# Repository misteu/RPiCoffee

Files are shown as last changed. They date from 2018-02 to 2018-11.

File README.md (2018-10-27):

# RPiCoffee aka Coffee as a Service 4 real
Modding / hacking of a coffee machine (DeLonghi ECAM 22.110.B Magnifica S) for IoT capabilities 

See github-Page or docs/README.md for working progress: https://misteu.github.io/RPiCoffee/

Here is everything a little bit more detailed: https://github.com/misteu/RPiCoffee/wiki (<-- still a lot of stuff missing, coming soon!)

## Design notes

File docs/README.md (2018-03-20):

# RPiCoffee

This project's goal is to make a coffee machine responsive to different HTTP-Requests, like:

**JSON-Request**
```json
{
  "userID": "admin",
  "actions": [
    "turn on",
    "brew espresso"
  ]
}

```
'Cause nobody likes to wait for the machine.

_in fact: There are no JSONs involved right now :-D (see section "A little bit about [...]") Maybe in near future I will design a RESTful API supporting some cool JSON-responses like the one above_

see the project's wiki for more detailled information: [https://github.com/misteu/RPiCoffee/wiki](https://github.com/misteu/RPiCoffee/wiki)

**Possible scenarios are:**
- turn on and shutting down the machine via HTTP-request
- brewing single and double espresso via HTTP-request
- brewing single and double coffee via HTTP-request
- starting the rinse program via HTTP-request (good for preheating the system)
- chaining simple actions like in the example above
- reading out machine status (e.g. water level, coffee bean depot, temperature, errors, ...)
- rendering a responsive web-app for better user experience
- data logging and visualisation in the web-app

### Intro ###
The easiest way is to hack the existing frontpanel via overriding its pushbuttons. The HTTP-stuff can be handled by a microcontroller with a wifi-shield or a microcomputer like the the RaspberryPi Zero W which has built-in wifi.

I will stick to the Raspberry because it is cheap (around 12 Eur for the Zero W) and I do not have to make any hardware modifications to get it up and running. The Raspberry will be prepared with a minimal setup based on Raspbian Lite with everything unnecessary turned off. 

It's described in this article: [https://www.heise.de/ct/ausgabe/2017-22-Digitales-Flugblatt-Raspberry-Pi-mit-Batterie-als-anonymer-WLAN-Hotspot-und-Webserver-3851689.html](https://www.heise.de/ct/ausgabe/2017-22-Digitales-Flugblatt-Raspberry-Pi-mit-Batterie-als-anonymer-WLAN-Hotspot-und-Webserver-3851689.html)

The RPi will be powered by its own USB-power supply because I do not know how stable the coffee machines DC rails. Maybe later I will parallel the 230V rails of the coffee machine to the Raspberry's AC power supply.

On the RPi there will be running Flask for the HTTP-stuff and maybe a mongodb database for some data collecting.

### Mobile / Responsive User Interface stuff

#### WebApp-UI talking to the hardware
I combined my html+skeleton prototype with some Flask and the LED() function of the Python module gpiozero. In the animation below you can see one of the first iterations. All the buttons of the machine's front are accessible programatically right now. The "steam button" is not implemented in the WebApp because in general it is never used.

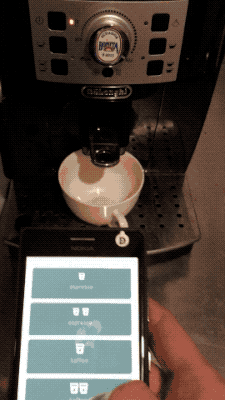
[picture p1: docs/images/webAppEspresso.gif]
animation of brewing espresso via Web App


The feature menus (statistics, settings and mining) are not implemented right now. I implemented a small java script popup to inform the user about that when one of these buttons is clicked.

I already installed mongoDB on the raspberry to save statistics and settings and made some first experiments.

+++ update +++

Instead of the fun but pretty useless mining, there is now implemented an info screen with train departure times. See section "API-Calls [...]" in my wiki.

#### Second iteration: WebApp-UI
I made a redesign of the UI because I did not like the dark theme (see below). I began prototyping the complete thing in Sketch and transfered it later to HTML and CSS with the help of Skeleton ([getskeleton.com](http://www.getskeleton.com)) and Sketch's CSS and SVG output-features. 

I picked a nice morning like gradient from [webgradients.com](http://webgradients.com) and played around with colorsets from [coolors.co]. For the final touch I added these transparent triangle things for some foggy morning effects. They are technically stacked CSS3 clipping paths of div-elements I colored with #fff and alpha = 0.2 ;-)

The icons are this time from Google's material design icon-font ([https://material.io/icons/](https://material.io/icons/)) I found them via the awesome iconfont plugin for Sketch by Kerem Sevencan ([https://github.com/keremciu](https://github.com/keremciu))

All the hover interaction-stuff and responsiveness is finished. Everything else (settings, stats and cryptomining😅) will be added iteratively as soon as main functionalities are up and running.

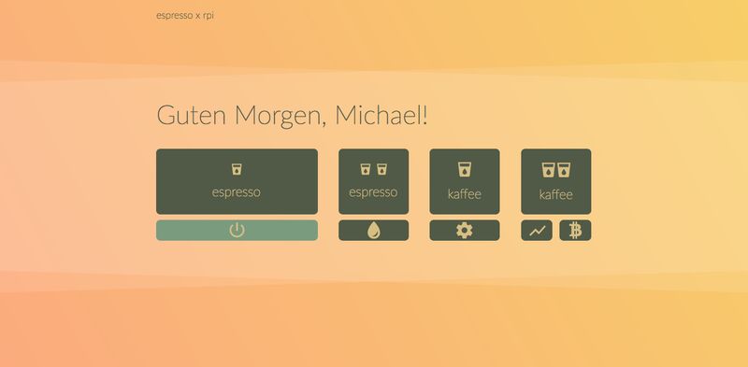
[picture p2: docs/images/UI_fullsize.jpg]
Image of new UI


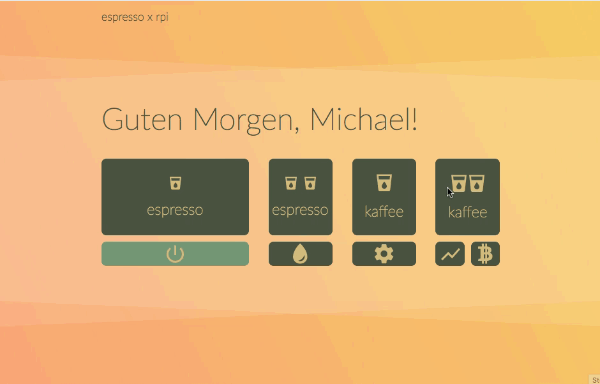
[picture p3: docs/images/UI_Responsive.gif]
Image of new UI


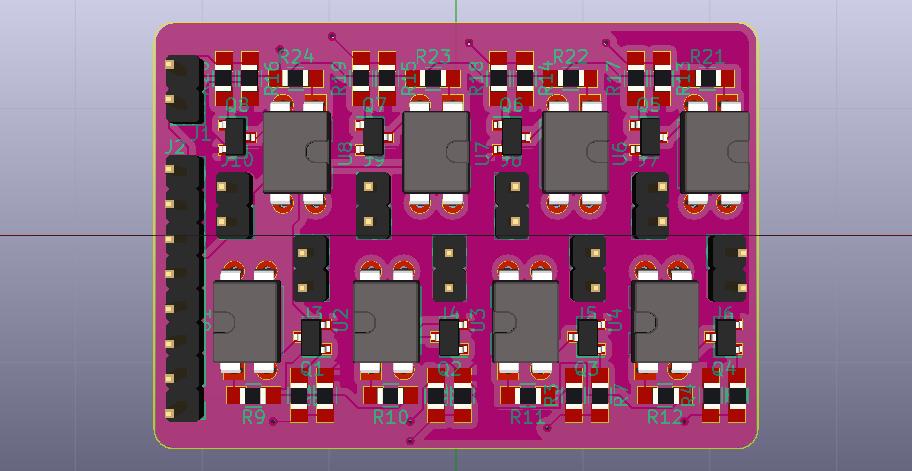
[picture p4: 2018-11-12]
schematics_KiCadProject/kaffeeInterface.jpg

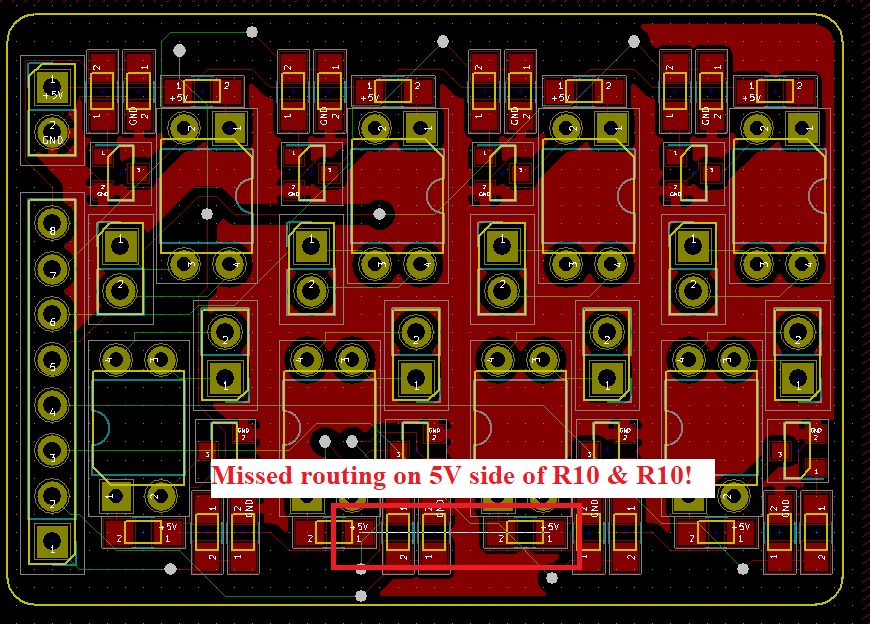
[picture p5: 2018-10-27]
schematics_KiCadProject/missedRouting.jpg

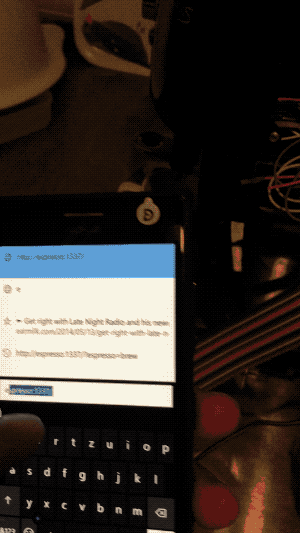
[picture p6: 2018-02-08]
docs/images/Flask_to_espresso.gif

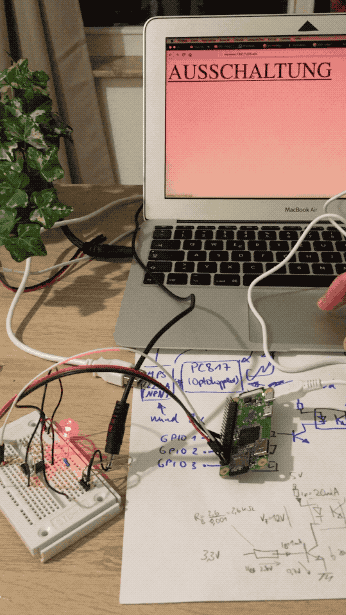
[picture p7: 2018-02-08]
docs/images/Flask_to_GPIO.gif

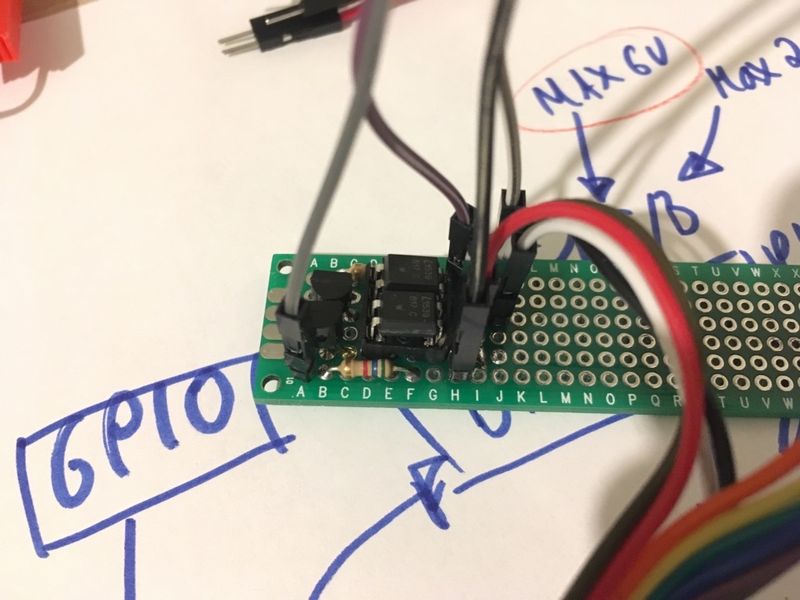
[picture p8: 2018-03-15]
docs/images/Optocoupler_circuit.jpg

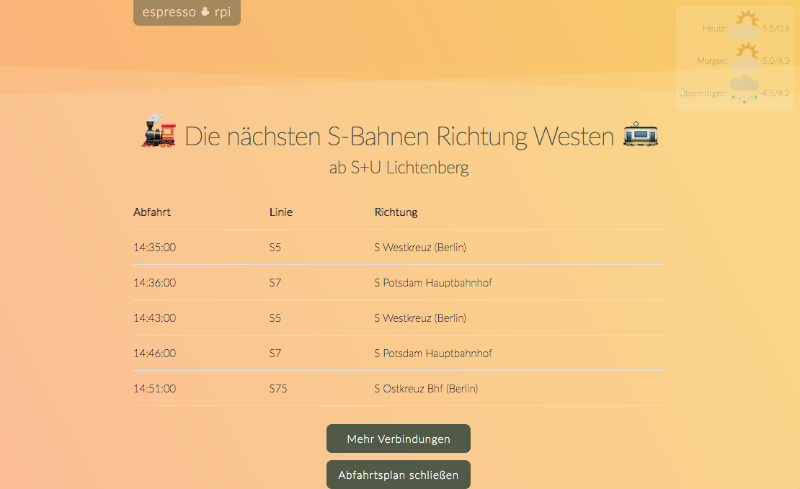
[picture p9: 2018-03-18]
docs/images/UI_metro_widget.png

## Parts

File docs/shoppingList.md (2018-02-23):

### Raspberry and power supply
1x Raspberry Pi Zero W 13,50€ (inkl. Versand, von pimoroni)
1x NT MUSB 2 WS
USB-Ladegerät, 5 V, 2000 mA, Micro-USB
6,00 €

### other stuff from reichelt (for the interface circuit)

3x
MOS 4051
CD4051BE
0,90 €

15x
LTV 817
OPTOKOPPLER
2,86 €

20x
BC 547A CDIL
Transistor NPN TO-92 45V 0,1A 0,5W
0,60 €

20x
1/4W 1,0K
Widerstand, Kohleschicht, 1,0 kOhm, 0207, 250 mW, 5%
0,67 €

20x
1/4W 4,7K
Widerstand, Kohleschicht, 4,7 kOhm, 0207, 250 mW, 5%
0,67 €

20x
1/4W 200
Widerstand, Kohleschicht, 200 Ohm, 0207, 250 mW, 5%
0,67 €

20x
1/4W 5,6K
Widerstand, Kohleschicht, 5,6 kOhm, 0207, 250 mW, 5%
0,67 €

5x 
WAGO 221-413
Verbindungsklemme, 3-Leiteranschluss
2,40 €

1x
H05VK 0,75-10BR
Schaltlitze H05V-K, 0,75 mm, 10 m, braun
1,85 €

1x
H05VK 0,75-10BL
Schaltlitze H05V-K, 0,75 mm, 10 m, blau
1,75 €

1x
SDH 1,6 SW
10er Pack 2:1 Schrumpfschlauch, 1,6mm schwarz
0,25 €

1x
SDH 2,4 RT
10er Pack 2:1 Schrumpfschlauch, 2,4mm rot
0,32 €

1x
SDH 3,2 SW
10er Pack 2:1 Schrumpfschlauch, 3,2mm schwarz
0,26 €

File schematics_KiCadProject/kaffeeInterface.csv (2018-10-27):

ID | Bezeichner | Gehäuse | Stückzahl | Bezeichnung | Anbieter und Ref.
1 | J1,J3,J4,J5,J6,J7,J8,J9,J10 | Pin_Header_Straight_1x02_Pitch2.54mm | 9 | Conn_01x02_Male
2 | J2 | Pin_Header_Straight_1x08_Pitch2.54mm | 1 | Conn_01x08_Male
3 | Q1,Q2,Q3,Q4,Q5,Q6,Q7,Q8 | SOT-23 | 8 | BC847
4 | R1,R2,R3,R4,R13,R14,R15,R16 | R_0805_HandSoldering | 8 | 10k
5 | R5,R6,R7,R8,R17,R18,R19,R20 | R_0805_HandSoldering | 8 | 5,6k
6 | R9,R10,R11,R12,R21,R22,R23,R24 | R_0805_HandSoldering | 8 | 200
7 | U1,U2,U3,U4,U5,U6,U7,U8 | DIP-4_W7.62mm | 8 | LTV-817

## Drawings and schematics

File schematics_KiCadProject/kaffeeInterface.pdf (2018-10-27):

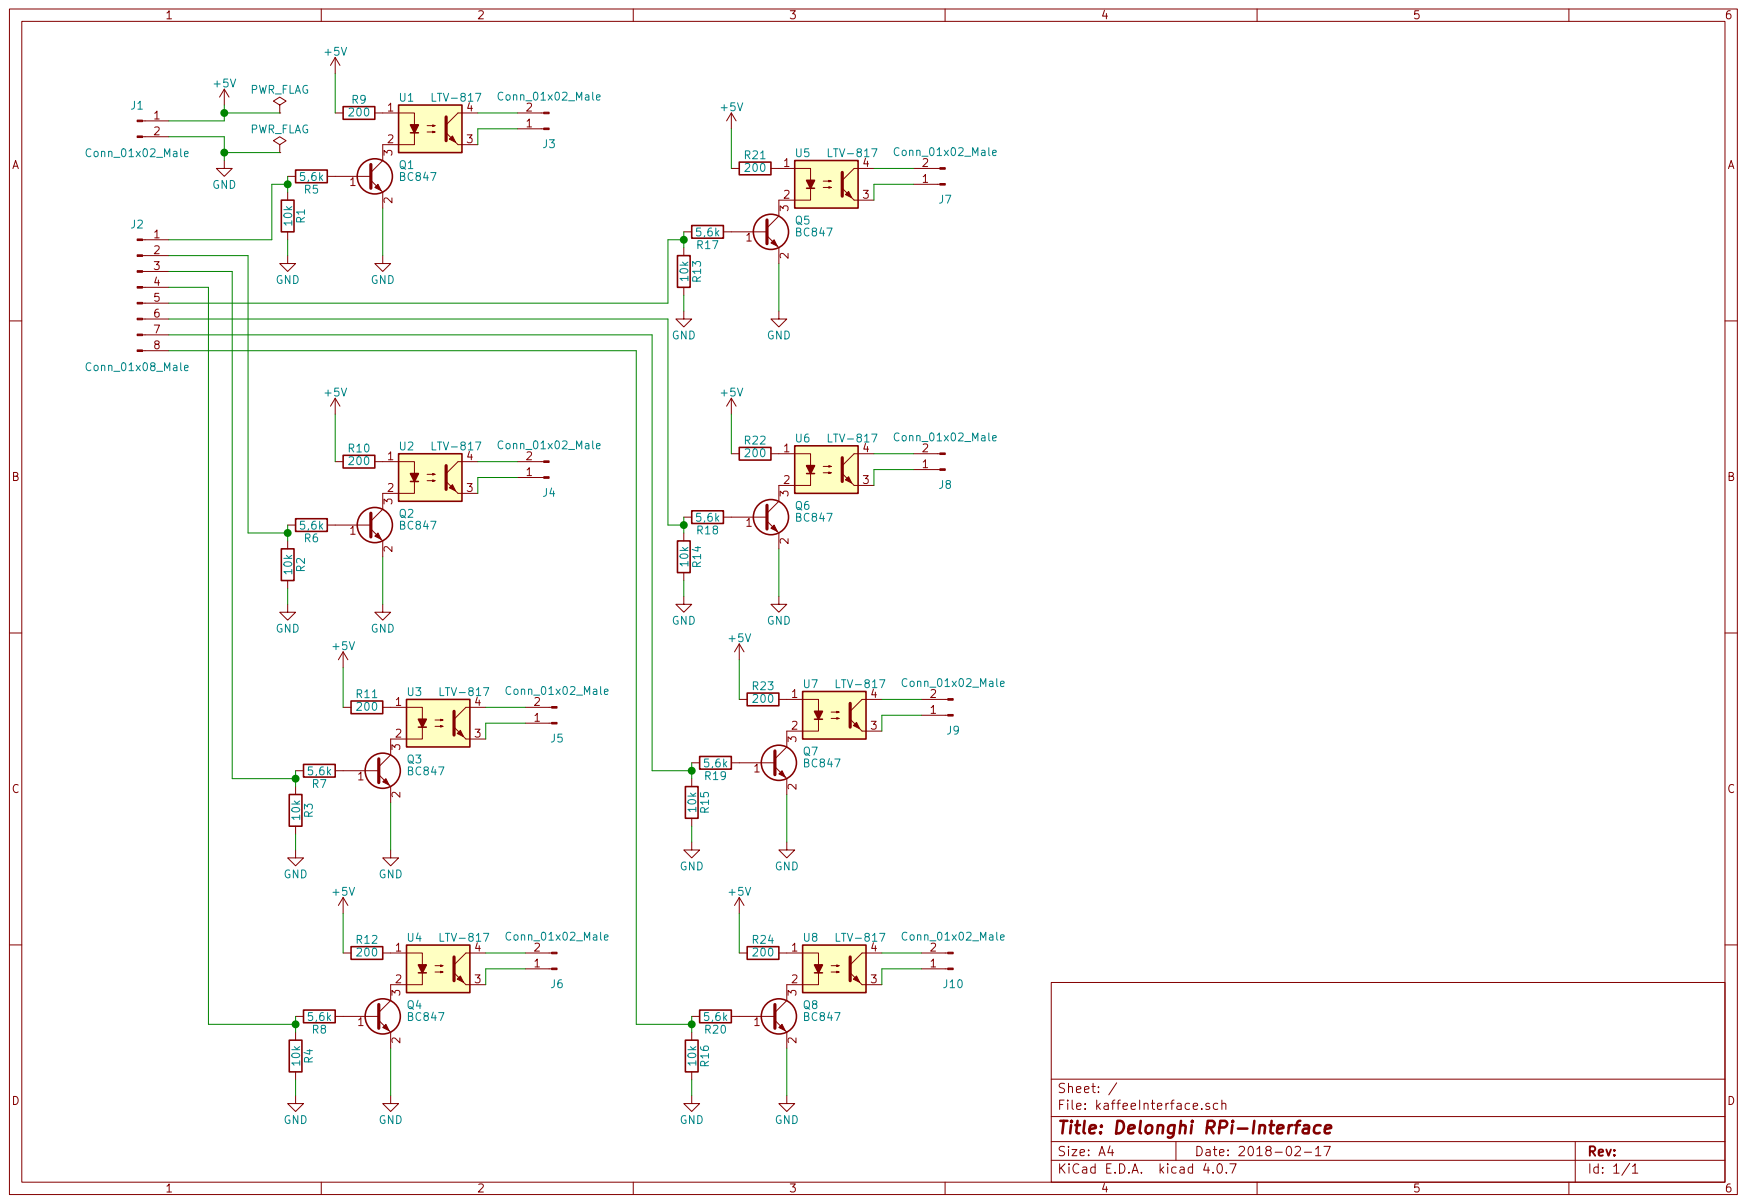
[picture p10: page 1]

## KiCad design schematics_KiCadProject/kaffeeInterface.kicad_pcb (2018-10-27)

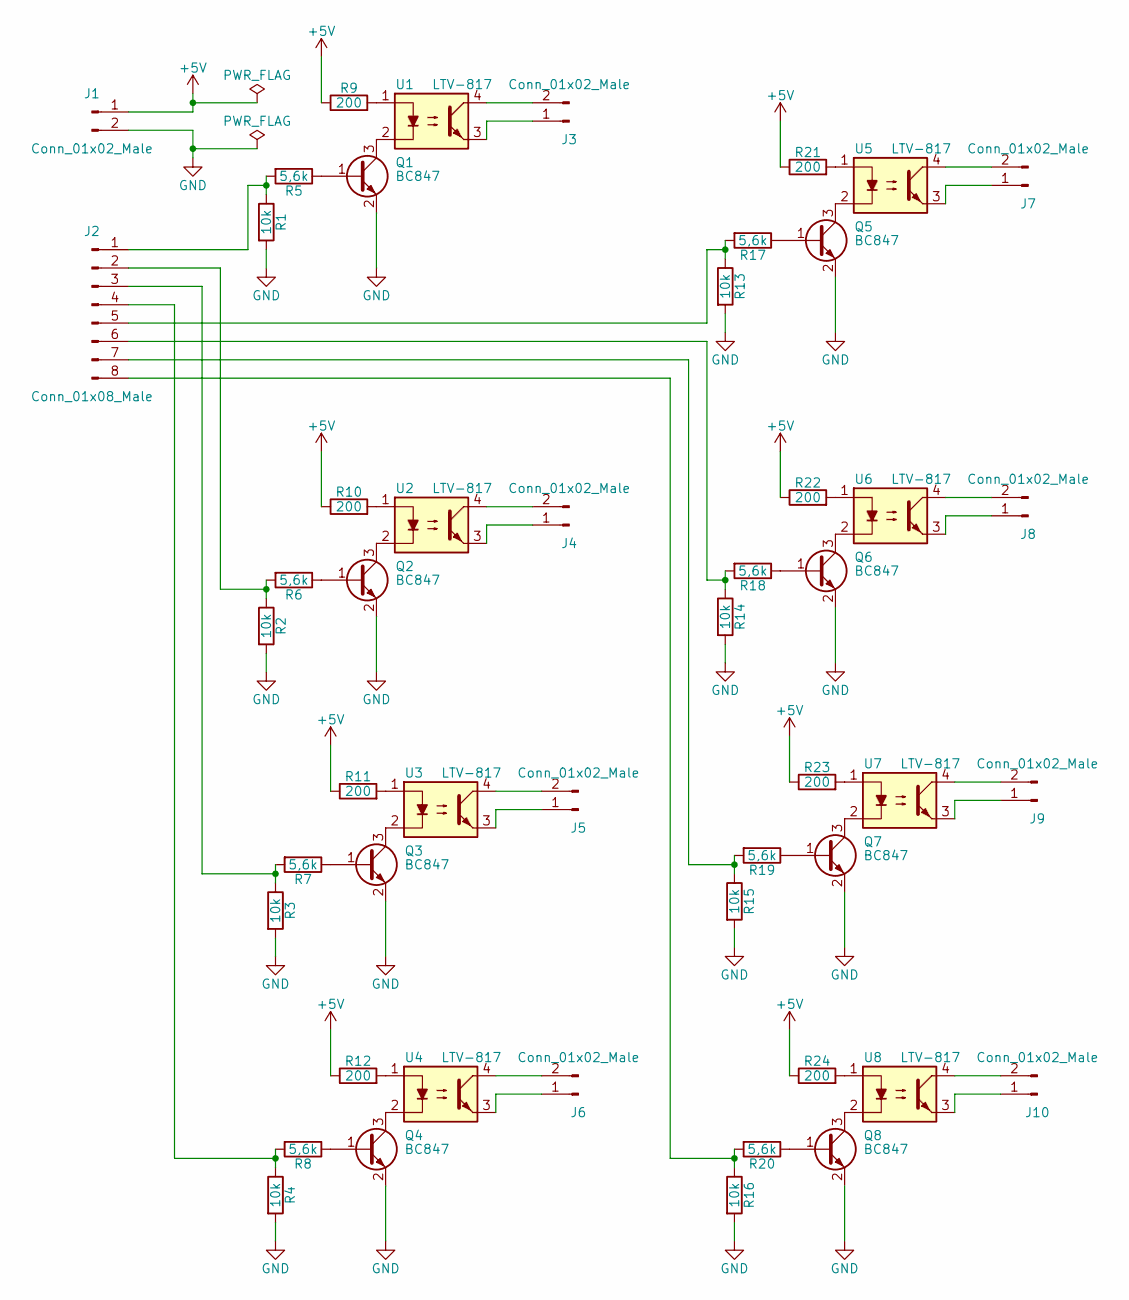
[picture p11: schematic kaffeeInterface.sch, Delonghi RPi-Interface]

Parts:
J1, J3, J4, J5, J6, J7, J8, J9, J10: Conn_01x02_Male; Pin_Header_Straight_1x02_Pitch2.54mm
J2: Conn_01x08_Male; Pin_Header_Straight_1x08_Pitch2.54mm
Q1, Q2, Q3, Q4, Q5, Q6, Q7, Q8: BC847; SOT-23
R1, R2, R3, R4, R13, R14, R15, R16: 10k; R_0805_HandSoldering
R5, R6, R7, R8, R17, R18, R19, R20: 5,6k; R_0805_HandSoldering
R9, R10, R11, R12, R21, R22, R23, R24: 200; R_0805_HandSoldering
U1, U2, U3, U4, U5, U6, U7, U8: LTV-817; DIP-4_W7.62mm

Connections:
+5V: J1.1, R9.1, R10.1, R11.1, R12.1, R21.1, R22.1, R23.1, R24.1
GND: J1.2, Q1.2 (E), Q2.2 (E), Q3.2 (E), Q4.2 (E), Q5.2 (E), Q6.2 (E), Q7.2 (E), Q8.2 (E), R1.2, R2.2, R3.2, R4.2, R13.2, R14.2, R15.2, R16.2
unnamed: J2.1, R1.1, R5.2
unnamed: J2.2, R2.1, R6.2
unnamed: J2.3, R3.1, R7.2
unnamed: J2.4, R4.1, R8.2
unnamed: J2.5, R13.1, R17.2
unnamed: J2.6, R14.1, R18.2
unnamed: J2.7, R15.1, R19.2
unnamed: J2.8, R16.1, R20.2
unnamed: J3.1, U1.3
unnamed: J3.2, U1.4
unnamed: J4.1, U2.3
unnamed: J4.2, U2.4
unnamed: J5.1, U3.3
unnamed: J5.2, U3.4
unnamed: J6.1, U4.3
unnamed: J6.2, U4.4
unnamed: J7.1, U5.3
unnamed: J7.2, U5.4
unnamed: J8.1, U6.3
unnamed: J8.2, U6.4
unnamed: J9.1, U7.3
unnamed: J9.2, U7.4
unnamed: J10.1, U8.3
unnamed: J10.2, U8.4
unnamed: Q1.1 (B), R5.1
unnamed: Q1.3 (C), U1.2
unnamed: Q2.1 (B), R6.1
unnamed: Q2.3 (C), U2.2
unnamed: Q3.1 (B), R7.1
unnamed: Q3.3 (C), U3.2
unnamed: Q4.1 (B), R8.1
unnamed: Q4.3 (C), U4.2
unnamed: Q5.1 (B), R17.1
unnamed: Q5.3 (C), U5.2
unnamed: Q6.1 (B), R18.1
unnamed: Q6.3 (C), U6.2
unnamed: Q7.1 (B), R19.1
unnamed: Q7.3 (C), U7.2
unnamed: Q8.1 (B), R20.1
unnamed: Q8.3 (C), U8.2
unnamed: R9.2, U1.1
unnamed: R10.2, U2.1
unnamed: R11.2, U3.1
unnamed: R12.2, U4.1
unnamed: R21.2, U5.1
unnamed: R22.2, U6.1
unnamed: R23.2, U7.1
unnamed: R24.2, U8.1

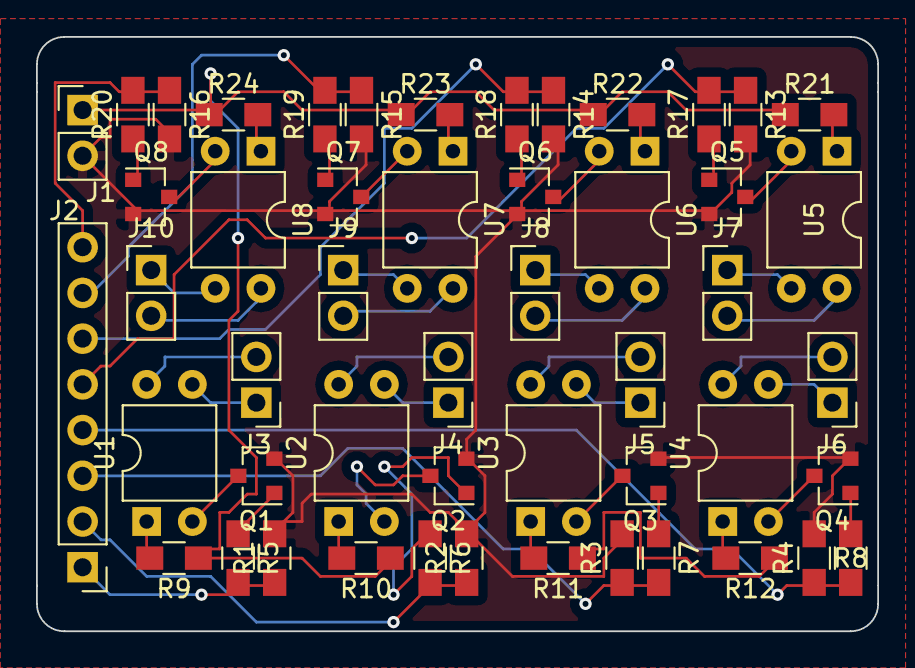
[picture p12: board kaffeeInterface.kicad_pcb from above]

Board: 2 copper layers, 46.7 x 33.0 mm, 50 parts (0 on the bottom side), 50 nets.

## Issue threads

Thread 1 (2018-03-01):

RFID payment system

adur1990, 2018-03-01:
Hi,

I had a somewhat similar idea with our coffee machine. We have the same DeLonghi machine. What we want to do is to have a system, which requires a RFID card to unlock the device. The normal buttons should not work anymore.

Now, we could do it with the same technique like you by interfacing the buttons, but it would be great, if we could reverse engineer the firmware and modify it like we want. And I saw in your todo list, that you also plan to interface all sensors and so on.

We have the schematics of the machine and the firmware (the schematics are in german, but as I can see, you are from Berlin). I will attach both to this issue. Maybe we can join forces :)
[DeLonghi_Magnifica_ECAM22.110_CH00.pdf](https://github.com/misteu/RPiCoffee/files/1770720/DeLonghi_Magnifica_ECAM22.110_CH00.pdf)
[PIC18LF2520_ECAM22.110_SW1.2.zip](https://github.com/misteu/RPiCoffee/files/1770721/PIC18LF2520_ECAM22.110_SW1.2.zip)

misteu, 2018-03-15:
Hi there!
Sorry for my late reply, unfortunately I saw your nice comment onyl now! Although I made some updates on github meanwhile... I will have to change my notification settings on github :-D

Your idea sounds great! And: WOW! Your schematics will help so much for updates in near future!
Until now I measured everything bit by bit with my cheapo voltmeter ;D

Reverse engineering sounds pretty decent!
One of my first ideas was to grab the signals between the machine's mainboard and the front PCB. Then I could have used the flat wire and some interface between the front PCB and the mainboard. But in the end, my bridging (hammer-like) approach feeled much easier for me :)

For reading the machine's sensors and getting feedback in general, the reverse engineering would be really, really nice.

On the other hand, I do not know if there is any real advantage of your second idea in modifying the firmware. In my opinion the results (espresso) of the machine's original behaviour are pretty good I think. Messing around with motor movements and so on bears the risk of crashing something more than electronics.

With my solution you could just cut or desolder the mechanical buttons and connect some RFID reader to the raspberry. Oh and I did not upload one of my schematics i do realize right now :-D
Will be added soon!

I will definitely use your schematics and look into your firmware. Thanks again! And I am totally into joining forces!

You have some experience with PICs? I did not yet look into the firmware but I spotted "PIC..." :-)

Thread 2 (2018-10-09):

Electronics tutorial

marciii, 2018-10-09:
Hi,

Ive seen this project and was really amazed and want to try it for my machine too.

However I have no clue about the electronics - how to connect the Pi and the machine in Detail.

Are you still planning to do a noob-friendly tutorial? Would ne awesome!

Cheers

rgerr, 2018-10-09:
+1, interested in this too.

rgerr, 2018-10-11:
Have checked out the shoppinglist, however it is incomplete. Firgured I would try and make it work through the pictures. But I can't seem to find the PCB board/interface where all the parts are soldered to.

misteu, 2018-10-26:
Sorry for my late response! I forgot to set any notifications on github.
Thank you very much for your feedback, it is nice to hear that you are interested!

Yeah, I will definitely work on a tutorial/rework the circuit diagrams. Currently, I am a little bit busy with my Masters thesis but I will find some time ;-)

marciii, 2018-10-26:
Nice, thanks!
And good luck with your thesis =)

rgerr, 2018-10-26:
Do you have the gerber files for the pcb? Then I can order it and try already!

misteu, 2018-10-27:
hi there,
I just uploaded the whole KiCad Project to the repo. My PCBs were made by Oshpark where you can upload your KiCad files directly without plotting gerber files. In case you want to use some other service, I exported the gerber plots in a separate folder.

I also included the schematic as PDF.

Please pay attention to the missing route between to resistor R10 and R11. I remarked that when the PCBs where already produced.  ou have to solder some wire by hand to fix that. I included a screenshot of KiCad where I marked that area. You can try to reroute it in KiCad or just fix it the same way ;)

Hope that helps so far!

misteu, 2018-10-27:
No it is not fixed.

You can fix it manually with soldering a wire as shown here: https://github.com/misteu/RPiCoffee/blob/master/schematics_KiCadProject/missedRouting.jpg

On that photo you can see how it looks on the finished PCB: https://github.com/misteu/RPiCoffee/blob/master/docs/images/PCB_soldered.jpg
So, pretty easy. If you managed to solder all the SMD stuff on the board, this one will be the most relaxing work ever 😅

If there is enough space on the PCB to fix that route, that would be the more elegant solution. But honestly, no one notices that PCB when it is built in 😄

rgerr, 2018-11-07:
Could you perhaps update the shopping list you created? Or it the shopping list actual, on Reichelt?

misteu, 2018-11-07:
hi there,
for soldering the interface circuit you just need the stuff I put into that table here in the wiki: https://github.com/misteu/RPiCoffee/wiki/Shopping-list

You will find all the parts if you search for them in your favorite electronics store. All of these are pretty common parts.

In addition to that you just need the RPI, a power supply and very thin wire as described in the wiki entry.

rgerr, 2018-11-08:
Thanks, ordered the PCBs. But I see that you updated the shopping list, now I am not able to find all the parts anymore on reichelt. Could you perhaps send me the actual reichelt list? Makes it allot easier to order for me.

misteu, 2018-11-10:
hi there.

You can still find everything on reichelt. Just type in the part number to the search field.

Pin headers straight are called "Stiftleiste" at reichelt. You can buy these: https://www.reichelt.de/rnd-stiftleiste-8-pol-rm-2-54-mm-rnd-205-00629-p208855.html?&trstct=pol_3

You can order them four times (1x 1x08 and 9x 01x02) and break them apart to get the 01x02 headers

The transistors (BC847) you need are these: https://www.reichelt.de/bipolartransistor-npn-45v-0-1a-0-3w-sot-23-rnd-bc847b-p223362.html?&trstct=pos_0
make sure you buy transistors with the case type called: SOT-23 (like in the link above)

The resistors you can find here: https://www.reichelt.de/0805/2/index.html?ACTION=2&LA=2&GROUPID=8397 You can find the right value via the filter on the left, you need 10k, 5.6k and 200 each one eight times. They cost pretty much nothing. So I would buy e.g. 100 of each value (1,2€ per value). They get lost easily and you can uses them for some other projects, too.

The optocouplers are these: https://www.reichelt.de/optokoppler-ltv-817-p76173.html?&trstct=pos_3

you can solder the optocouplers directly onto your PCB or use some sockets. I don't know if there are 4pin sockets available. I did not found them, so I cut apart these: https://www.reichelt.de/ic-sockel-8-polig-doppelter-federkontakt-gs-8-p8230.html?&trstct=pol_1

You can buy theses wires to connect/solder your front panel buttons to the interface PCB: https://www.reichelt.de/index.html?ACTION=446&LA=3&q=kupferlackdraht
I would not buy something thicker than 0.2mm because there is not much space if you want to connect all the buttons.

To connect the copper wires to your interface board's connectors I would use these wires, because they already have the right connector: https://www.reichelt.de/flexible-drahtbruecken-7-cm-buchse-buchse-10er-pack-steckboard-mbbvt-p177393.html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 just cut them apart and solder them to the copper wires.

Everything is pretty standard stuff so you could also look on ebay for cheaper offers. I ordered a lot of electronics parts on ebay.

I hope that helps.

rgerr, 2018-11-10:
Alright, thanks! So the parts you linked are all the parts I need, in the correct number?

misteu, 2018-11-10:
Yeah for the interface PCB that should work. I suggest you look at the circuit and do check if everything is on the list.

And of course you need the raspberry pi ;) You will also need some pin headers and jumper wires for connecting the raspberry pi to the interface PCB. There are also shops offering the raspberry pi with pre-soldered headers for a few euros more. If you buy a handful of jumper wires you have enough for soldering them to the copper wires and for connecting the PCB to your raspberry. Jumper wires with a length of 10cm are pretty good. I would buy 50 of them or something like that on ebay.

So I would not count every single piece of the circuit ;) Overall, the parts are pretty cheap, even if you buy everthing double ;)

rgerr, 2018-11-11:
Thanks! Ordered the parts. This is my first ‘big’ soldering project. Did a few small projects with Wemos and ESP8266.

Now when the parts are in, I can get started. Do you have a overview where I can easily see which part goes where?

misteu, 2018-11-11:
I looked in KiCad while soldering. Actually it's eight times the same circuit. So if you finished one or two of them you will know which part goes where ;-)

I reinstalled everything on my rpi today, because something crashed some weeks ago which made it inaccessible. I don't know why this did happen, maybe the logfiles grew to big or something like that.

Long story short: It's a good practice to make some kind of backup of your SD-card as soon as everything works. I didn't had that.. :( Spent some hours reinstalling everything by hand :-/
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
misteu, 2018-11-11:
ah nice! I didn't heard of Homebridge before :)

self-maintaining sounds great, I hacked something together on a fresh Raspian Jessie install.

haha I like that idea of connecting the machine via homebridge to siri 😄

rgerr, 2018-11-12:
Do you have a high resolution picture of the soldered PCB? I am having a hard time figuring out which goes where.

misteu, 2018-11-12:
Do you have KiCad installed? To look there is the safest way to solder the parts to the right spot.
There is also a 3D Model Viewer built-in. But I prefer the PCB view where you can just right click the connections and see which part goes there.

Anyway, I can make some photos today because I want to reinstall the updated RPI to the machine. But I can't promise high resolution pictures 😄

rgerr, 2018-11-12:
Currently, no. I will get to installing that. The KiCad files provided will generate a 3D model? That would be very helpful. The schematics are gibberish to me, when it comes to actually soldering the parts where they belong.

A few close up pictures of the circuits would be great, will make it a bit more 'alive'. :)

misteu, 2018-11-12:
The 3D view looks like this:
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

E.g. you can see that there is R23 directly above one of the optocouplers following R15 and R19 from right to left. All of these eight circuits follow the same pattern. I designed one of them and copied it eigth times, than routed everything.

If you look at the circuit diagram you can see the values of R23, R15 and R19:
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

rgerr, 2018-11-12:
I see, that makes it fairly easy to determine which goes where. Thank you! Reichelt just shipped my order, so hopefully it will arrive later this week for me to give it a try.

rgerr, 2019-03-27:
After several attempts, I did not succeed. Soldered three pcb’s according to the manual, with the correct resistors and such. Double checked everything, but no signal comes through.

However, when I connect the wires from the machines board (on/off button) to the pi zero directly, it does work. So it is safe to say the problem lies in the pcb. I am not that much of an electronics expert, so I am wondering what is wrong with connecting the wires from the machines board to the pi zero directly?

misteu, 2019-03-28:
Hi,
I'm sorry for that. You double checked every connection I assume? Maybe you damaged some transistor while soldering. They are pretty easy to destroy when heating up too much or too long. I remember that I dumped some of them when I had the feeling that I gave them too much heat.

I did not connect them directly for three reasons:

1. I did not want to mess around with (or think about) the machines signal levels. The RPi works with 3,3 or 5V, the machine: I don't know. The custom PCB separates both power supplies and both logical levels. The word for it is galvanic isolation, the optocouplers make sure that there is no current running between the machine and the PCB. If you connect the RPi directly to the machine, you could also get problems with noise and as a result very undefined switching of your buttons.
2. If there would be some short circuit in an RPi without galvanic isolation to the machine, the machines PCB could be damaged as a result of that short circuit.
3. The RPi's output drivers are not designed for directly driving loads permanently. The transistor makes sure that the outputs load is never above that limit for permanent loads.

rgerr, 2019-03-30:
Alright, so the PCB is necessary. Maybe an odd question, but since I cannot get it to work, would you be able to make the board? I am willing to pay for that, ofcourse!

misteu, 2019-03-30:
Currently, I am a litte bit busy writing my master thesis. I can't say for sure when I got time for it.

In general, I could do the soldering if you provide the parts needed. I have got spare parts from my build but I am not sure if there is enough of everything for a second one. I am a little bit low on optocouplers I think. If you take care of them I could do the soldering (on ebay they are pretty cheap).

Maybe you could send me your PCBs and I could also take a look at them first and run some tests on it. Maybe it's just some small error/broken part. It would be a pity to throw them all away, because this board could be user for a lot of projects connecting anything to a RPi (like relais and stuff like that).

rgerr, 2019-03-30:
That would be amazing! I think it would be better if we discuss this in private, so I can send you the parts. I will ofcourse send all the spares I have. Is there a private messaging on GitHub?

misteu, 2019-03-30:
I don't know but you can visit my website (mic.st) and scroll down to my email adress. I do not want to post it here due to spambots.

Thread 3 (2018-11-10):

Check and update the shopping list from circuit diagrams

misteu, 2018-11-10:
Currently there is not one single shopping list. The best way to find out what is needed is to look into the circuit diagram.

I posted some updates here: https://github.com/misteu/RPiCoffee/issues/2#issuecomment-437574930

If anybody got time, feel free to collect everything in one list ☺️

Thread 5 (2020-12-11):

Waste water?

basekson, 2020-12-11:
Sorry for make this an issue, did not find you contact info.
Do you have any good solution for the rinse/waste water that pumps out on boot?

If I make it with Google Assistant in the morning - Hey Google, make a double espresso.
Then It will boot up and rinse the water about 5-10 cl. Then this automation will be no good or do you have found out any good solution for this?

THANKS for all the nice guides!

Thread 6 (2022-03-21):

Question about electronics

nekromant, 2022-03-21:
Hello! Thanks for the awesome project! Can you share some higher quality pics of the display board? Especially the markings on the two ICs (They look like shift registers at first glance).

I recently got myself this coffee machine and I also plan to make it smart. However I decided on a different approach: I want to just redesign the board with leds and buttons to a custom-made with a esp8266(esphome) onboard so that it would just be a snap-in replacement.

Thanks!

misteu, 2022-09-28:
Hey!
Sorry that I saw your comment only now. I might have accidentally turned off notifications :(

As far as I remember, there is a maintenance manual flying around somewhere in the internet which has a lot (if not all) of the schematics.

If you google for "delonghi magnifica schematic" there is a lot of stuff coming up, maybe there is also what you need :)

nekromant, 2022-11-29:
It also took me a while to notice your response, so we're even ;)

Meanwhile I found this writeup, so the only thing remaining is just hooking a pcb and writing a esphome component, which is what I will be doing pretty soon.

https://stevep.xyz/2018/05/17/delonghi-magnifica-now-with-alexa/

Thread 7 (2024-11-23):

Schematic

kamahat, 2024-11-23:
Hello,

To help you going a bit further here is the link to the schematic of both board :
[schema-electrque-ecam22.110 (1).pdf](https://github.com/user-attachments/files/17879201/schema-electrque-ecam22.110.1.pdf)

wvries, 2025-01-13:
Thanks for this.
I see J9 connecting to the PI C 18F 2520 and exposing rx, tx and ground....
what if we could interface this to the ESp32 and decipher the protocol.
Maybe not even needed to do any soldering or anything else to get at statuses or commands.

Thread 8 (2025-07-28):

Documentation link offline

djansen1987, 2025-07-28:
Hi, this sould really great to do. I wanted to look at the steps i should take to open the machine and how to connect it, but it seems the link is offline. Is there a other place to find how to connect en configure this ?

https://www.heise.de/ct/ausgabe/2017-22-Digitales-Flugblatt-Raspberry-Pi-mit-Batterie-als-anonymer-WLAN-Hotspot-und-Webserver-3851689.html

misteu, 2025-07-28:
Hi @djansen1987 !

This link you mentioned did just lead to an article where the raspberry pi basic setup is explained.

It does not really have to do anything with the mod / hack itself. There is just a guide for getting the device up and running.

For opening the case, you just need the correct torx screwdriver / nut and open the screws at the back of the machine.

when sliding back the side panels you can remove them and see the interior.

djansen1987, 2025-07-28:
Thanks you, and where can I then find how you connected the wires and which components to use?

misteu, 2025-07-29:
Please have a look into the readme, there is a link to this github page: https://github.com/misteu/RPiCoffee/wiki

Inside of the electronics section there is some more information.

It’s based on a board I designed in KiCad. You can order all the parts an solder them onto it.

Unfortunately, the whole project‘s documentation is not really polished. Please ask if you have any further specific questions, I will try to help.

Doezer, 2025-08-16:
I second that, the link might be unavailable outside germany or something like this. I made a pull request to change the link with the one you gave #9

misteu, 2025-08-16:
Thanks for the PR!

Merged it

Closed 2025-08-16.

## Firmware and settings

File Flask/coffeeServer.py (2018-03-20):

from time import sleep, gmtime, strftime
from flask import Flask, request, jsonify, url_for, send_from_directory, send_file, render_template
import requests, datetime
# to read last line of file
from subprocess import check_output
from pymongo import MongoClient

# Define IP and port for Flask-server
HOST = '0.0.0.0'
PORT = 8000

rpiMode = bool(True)

print(strftime("%Y-%m-%d %H:%M:%S", gmtime()))

# to mongoDB
client = MongoClient()
client = MongoClient('localhost', 27017)

# define a database at mongoDB
db = client.rpiDB

# define collection inside rpiDB
coffee = db.coffee
rpiIP = "http://0.0.0.0:8000/"

# define debug Messages
message = {}
message["onOff"] = "Maschine faehrt hoch oder runter!"
message["espressoX1"] = "Einfacher Espresso im Bau!"
message["espressoX2"] = "Doppelter Espresso im Bau!"
message["steam"] = "Dampfmaschine am Laden!"
message["clean"] = "Saeuberung gestartet!"
message["coffeeX2"] = "Doppelter Kaffee im Bau"
message["coffeeX1"] = "Einfacher Kaffee im Bau"


if rpiMode:
	from gpiozero import LED
	PORT = 80

	rpiIP = "http://192.168.178.37:80/"

	# Define Espresso outputs as dictionary
	outputs = {}

	# GPIO 10 is currently not used

	# Turn machine on/off: blue wires
	outputs["onOff"] = LED(26)

	# Single espresso: white wires
	outputs["espressoX1"] = LED(19)

	# Prepare steam: yellow wires
	outputs["steam"] = LED(9)

	# Run clean program: gray wires
	outputs["clean"] = LED(11)
	
	# Double coffee: green wires
	outputs["coffeeX2"] = LED(12)

	# Single coffee: orange wires
	outputs["coffeeX1"] = LED(21)

	# Double espresso: violet wires
	outputs["espressoX2"] = LED(13)

def writeDB(data):
	coffee = db.coffeeCollection
	result = coffee.insert_one(data).inserted_id
	return result

def readDB():
	coffee = db.coffeeCollection
	result = []
	for action in coffee.find():
		#action['time'] = strftime("%a, %d %b %Y %H:%M:%S", action['time'])
		result.append(action)
	return result


def readAPIKeys():

	key = {}
	
	# Open a file
	file = open("apiKey.txt", "r")
	key['hafas'] = file.readline().rstrip('\n')
	key['suprnova'] = file.readline().rstrip('\n')
	key['suprnovaId'] = file.readline().rstrip('\n')
	file.close()
	print key
	return key

apiKeys = readAPIKeys()

apiKey_hafas = apiKeys['hafas']
apiKey_suprnova = apiKeys['suprnova']
apiId_suprnova = apiKeys['suprnovaId']


def getWeather():
	r = requests.get('https://www.metaweather.com/api/location/638242/')

	data = r.json()['consolidated_weather']

	return data


def getNextTrains():

	trains = []
# https://www.programmableweb.com/api/berlin-public-transport-rest
# Station S+U Lichtenberg, next Station = Noeldner Platz, show three results

	r = requests.get('https://2.vbb.transport.rest/stations/900000160004/departures?nextStation=900000160003&results=5')
	data = r.json()

	# Schnellere API --> Testen
	# r = request.get('http://demo.hafas.de/openapi/vbb-proxy/departureBoard?id=900160004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')


#print(strftime("%Y-%m-%d %H:%M:%S", gmtime()))

	for train in data:

		hour = train['when'].split("T")[1].split(":")[0]
		minute = train['when'].split("T")[1].split(":")[1]

		trains.append(
			{
			"direction":train['direction'],
			"line":train['line']['name'],
			"departure":"{}:{}".format(hour,minute)
			})

	return trains


def getNextTrainsHafas(lines, directions, length):

	lengthCount = 0
	trains = []
	r = requests.get('http://demo.hafas.de/openapi/vbb-proxy/departureBoard?id=900160004&accessId={}&format=json'.format(apiKey_hafas))
	data = r.json()['Departure']

	print('getNextTrainsHafas')
	for train in data:
		if train['Product']['line'] in lines and train['direction'] in directions:
			print(train['rtTime'], train['Product']['line'], train['direction'])

			trains.append(
			{
			"direction":train['direction'],
			"line":train['Product']['line'],
			"departure":train['rtTime']
			})
			lengthCount += 1

		if lengthCount >= length:
			break

	return trains


def getClientName(clientIPStr):

	clientIP = clientIPStr.split(".")
	
	clientIP = int(clientIP[3])

	if (clientIP == 42) or (clientIP == 47):
		print("e")
		name = "Eike"

	elif (clientIP == 23) or (clientIP == 46) or (clientIP == 36):
		print("m")
		name = "Michael"

	else:
		print("guest")
		name = "Gast"

	return name



app = Flask(__name__)



# Rendering UI at GET-Method
@app.route("/", methods=['GET'])
def renderUi():

	weather = getWeather()

	weatherIcon1 = weather[0]['weather_state_abbr']
	weatherIcon2 = weather[1]['weather_state_abbr']
	weatherIcon3 = weather[2]['weather_state_abbr']

	tempMinMax1 = "{}/{}".format(round(weather[0]['min_temp'],1),round(weather[0]['max_temp'],1))
	tempMinMax2 = "{}/{}".format(round(weather[1]['min_temp'],1),round(weather[1]['max_temp'],1))
	tempMinMax3 = "{}/{}".format(round(weather[2]['min_temp'],1),round(weather[2]['max_temp'],1))

	hashrate = 0
	status = ""
	price_usd = 0
	display_trains = "none"
	display_mining = "none"
	display_stats = "none"
	# balanceConf = 0
	# balanceUnconf = 0
	# balanceConfEUR = 0
	# balanceUnconfEUR = 0
	price_eur = 0
	creditEUR = 0
	credit = 0
	trains = []
	strompreisRPiTagEUR = 0
	arbeitspreis = 0
	greeting = bool(True)
	showMore = bool(False)
	stats = {}


	try:
		clientIP = request.remote_addr
		print(clientIP)
		name = getClientName(clientIP)

	except:
		print("could not read remote IP")


	## request Mining stats
	try:

	
		headline = "Guten Morgen {}".format(name)


		request.args['infos']
		if request.args['infos'] == "show":

			
			# Alternativer (langsamer) API-Call
			# trains=getNextTrains()

			try:
				mining = bool(False)
				request.args['mining']
				if request.args['mining'] == "show":
					mining = bool(True)
			except:

				try:
					request.args['showMore']
					if request.args['showMore'] == "true":
						length = 100
						showMore = bool(True)
				except:
					length = 5
					showMore = bool(False)

				lines = ["S5","S7","S75"]
				directions = ["S Westkreuz (Berlin)", "S Westkreuz (Berlin)", "S Potsdam Hauptbahnhof","S Ostkreuz Bhf (Berlin)"]
				trains = getNextTrainsHafas(lines, directions, length)


			if mining:
				r = requests.get('https://xmg.suprnova.cc/index.php?page=api&action=getuserstatus&api_key={}&id={}'.format(apiKey_suprnova, apiId_suprnova))
				validShares = r.json()['getuserstatus']['data']['shares']['valid']
				hashrate = r.json()['getuserstatus']['data']['hashrate']
				sharerate = r.json()['getuserstatus']['data']['sharerate']
				status = check_output(['tail', '-1', '../miner.out'])
				headline = "Mining Informationen"

				#
				# rBalance = requests.get('https://xmg.suprnova.cc/index.php?id=201792128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')
				# balanceConf = rBalance.json()['getuserbalance']['data']['confirmed']
				# balanceUnconf = rBalance.json()['getuserbalance']['data']['unconfirmed']
				#
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

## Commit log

2018-02-07 added UI-Prototype images
2018-02-07 renamed UI-Prototype images
2018-02-21 update enamelled copper wires
2018-02-22 skeleton powered UI finished
2018-02-23 buttons svgtext --> html
2018-10-27 added schematics
    [kaffeeInterface.dsn, kaffeeInterface.kicad_pcb, kaffeeInterface.sch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]
2018-10-27 added PDF of schematic
2018-10-27 added gerber plots
    [kaffeeInterface-B.CrtYd.gbr, kaffeeInterface-B.Cu.gbr, kaffeeInterface-B.SilkS.gbr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]
2018-10-27 added bom
    [kaffeeInterface.csv]
2018-11-12 Screenshot 3D PCB
2019-09-26 added annotated pcb

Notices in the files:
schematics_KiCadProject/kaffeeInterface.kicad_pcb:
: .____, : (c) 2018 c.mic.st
